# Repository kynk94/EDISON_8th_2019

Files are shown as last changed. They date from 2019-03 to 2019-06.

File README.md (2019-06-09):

# EDISON_8th_2019 - 두돈반

제 8 회 EDISON 전산설계  
  
팀명 - 두돈반  
팀장 - 강인구  
팀원 - 강인구, 기인호, 김은규, 서혁준

EDISON 8th(2019)  
Computational design Competition

## 3D 프린팅 모델


## 완성품


## 사용 부품 목록
Arduino UNO - 1 pcs  
Arduino UNO Protoshield - 1 pcs  
L298N Motor Driver - 1 pcs  
DM-CLS130TD Servo-Motor - 2 pcs  
Abrasive rod L:100mm D:5pi - 1 pcs  
과학상자 100-A Geared DC-Motor - 2 pcs  
과학상자 Gear No.106 - 2 pcs  
KOREAN : TCRT5000 IR Sensor (Mechasolution_hangul Manufatured) - 6 pcs  
TCS34725 Color Sensor - 1 pcs  
HC-SR04 Ultrasonic Sensor - 1 pcs  
1300mah LiPo Battery - 1 pcs  

## 동작 영상 (D-1) (대회 당일 영상이 없음)
<a href="http://www.youtube.com/watch?feature=player_embedded&v=sRzWvdurW9Q" target="_blank">
 IMAGE ALT TEXT HERE
</a>

## 대회 개요








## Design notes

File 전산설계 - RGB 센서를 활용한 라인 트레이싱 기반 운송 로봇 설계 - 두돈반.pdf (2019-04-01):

제8회 EDISON SW 활용 경진대회

## RGB 센서를 활용한

## 라인 트레이싱 기반 운송 로봇 설계

강인구, 기인호, 김은규, 서혁준

연세대학교 기계공학과
E-mail : kynk94@naver.com, dlghrnem@yonsei.ac.kr, dhdlrkawk1@naver.com, gurwns0904@naver.com

초록 : 본 논문은 비전 센서를 사용하지 않으면서 장애물의 색깔을 인식하여

지정된 미션을 수행하는 로봇을 제작한다. 아두이노를 활용한 차량의 라인

트레이싱을 위한 센서와 장애물을 옮기기 위한 메커니즘의 최적 설계를 수행한

모델을 제안한다.

1.서론

본 연구에서는 크게 운송을 위한 집게 형상
설계와 라인 트레이싱을 위한 센서 설계, 두
부분의 최적 설계를 제시한다. EDISON에서
제공하는 소프트웨어를 활용하여 안정적으로
운송이 가능한 운송 로봇을 설계한다. 또한
구동 시 고려해야하는 변수들을 직접 만든
프로그램을 활용하여 최적의 방식을 찾고,
이를 이용해 로봇의 설계를 진행한다.
본 논문의 구성은 다음과 같다. 2장에서
운송 로봇 설계 과정을 설명하고, 3장에서는
라인 트레이싱 제어, 색 인식과 관련된
센서들의 선정 및 설계 방법을 소개하고,
마지막으로 | 결론 | 및 | 논의사항에 | 대해서
서술한다.

2.운송 로봇 설계

### 2.1 집게 메커니즘

본 연구의 주 목표 및 설계 조건, 그리고
제작 및 분석 결과는 다음과 같다.
1) 주 목표 및 설계 조건
본 연구는 RGB센서와 아두이노를 활용한

선을 따라 자율 주행하는 라인 트레이싱
기반의 운송 로봇 설계를 주제로, EDISON이 제공하는 여러 소프트웨어들과 다른 부가적인
프로그램들을 | 활용하여 | 빠르게 | 미션을
수행하면서 | 안정적으로 | 라인 | 트레이싱을
하도록 설계하는 것을 목표로 한다.
지정된 설계 조건으로는 크게 세 가지가
있다. 첫째, 차량의 구동부는 과학상자에서
제공되는 No.100A 모터를 사용하며, 전원은 6V / 2.5A 로 공급한다. 둘째, 로봇에 사용될 기구는 과학상자 부품들, 3D프린터, 아크릴
등을 활용해 제작하며, 기구의 크기는 400mm x 400mm x 400mm 이내로 제작한다. 셋째,
제어부는 | 아두이노를 | 기반으로 | 제작하며,
센서는 총 15만원 이내에서 사용할 수 있다.
2) 모델링 결과

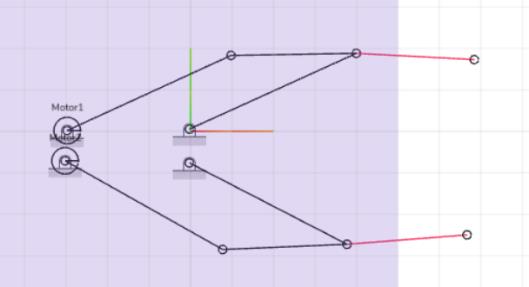
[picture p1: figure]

Figure 1. m.Sketch 링크 메커니즘

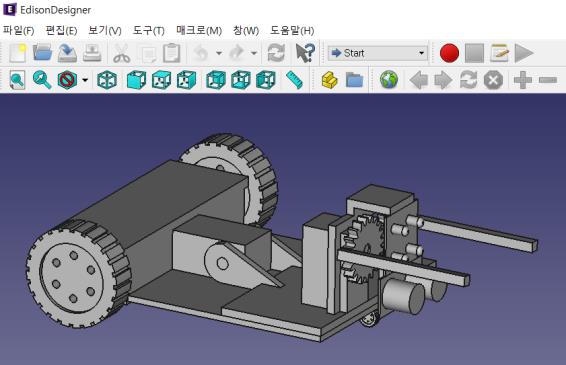
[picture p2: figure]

Figure 1. EDISON desginer 메커니즘

### 3. 로봇 센서 설계

### 3.1 라인트레이싱 메커니즘

본 메커니즘은 적외선 센서를 활용하여
라인 트레이싱을 하는 것이 목표이다.
1) 원리
라인 트레이싱에 필요한 최소 센서 개수는
2개이다. 이와 같은 기준으로 네 가지 경우의
수로 나누어진다. (1) 왼쪽 센서 인식, (2) 오른쪽 센서 인식, (3) 두 센서 모두 인식X, (4) 두 센서 모두 인식 이렇게 4가지 경우로
구분된다. 먼저 (1)의 경우는 차체의 왼쪽에서
라인을 | 인식했으므로, | 차체를 | 왼쪽으로
회전하여야 | 한다. | (2)는 | (1)과 | 반대로
오른쪽으로 회전하여야 한다. (3)은 라인이
두개의 센서 사이에 위치하므로, 직진하여야
한다. | 마지막으로 | (4)의 경우 정지하거나,
갈림길에서 원하는 특정 길을 선택할 수 있다.

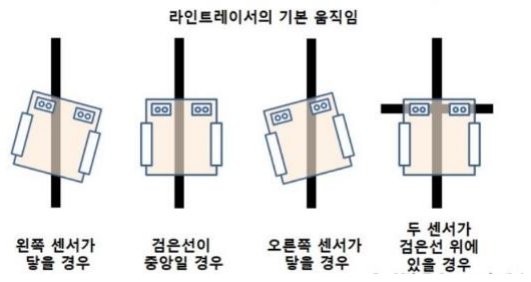
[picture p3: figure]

Figure 3. 라인 트레이싱 기본 원리

2) 알고리즘 설계
본 연구에서는 총 다섯개의 적외선 센서를
사용하여 | 아래의 | 메커니즘으로 | 라인
트레이싱을 하였다.
총 4가지 경우의 수로 나누어 설계하였다.
첫번째로, 3번 센서가 인식이 된 상태에서 2번 센서가 인식이 되면 차량이 라인의 오른쪽에
치우쳐져 있는 상태이므로 좌회전을 하였다.
4번의 센서가 인식이 되면 반대로 우회전을
하였다. 또 3번 센서만 인식되면 라인에
알맞게 있는 상태이므로 직진을 하였다. 모든
센서가 동시에 인식되는 미션 B의 끝과
라인으로 복귀할 때 만나는 교차로의 경우
서로 다른 행동을 해야하기 때문에, 모든
센서가 동시에 들어오는 첫 1회만 정지하고
그 다음은 좌회전하도록 설계하였다. 또는
모든 센서가 인식이 되지 않는 미션 C의
끝에서는 라인이 끝나는 지점이므로 정지를
하였다.

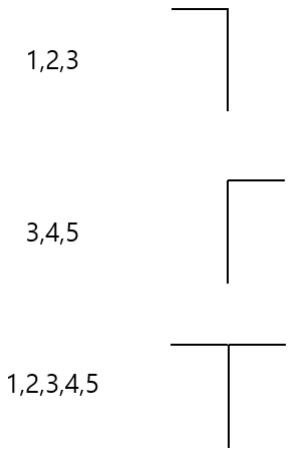
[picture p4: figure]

Figure 4. 교차로 인식 메커니즘

교차로를 인식할 때의 메커니즘은 총 3가지
경우의 수로 나누어 설계하였다. 1,2,3 센서만 인식이 되는 경우에 왼쪽 교차로로 인식을
하였다. 3,4,5 센서만 인식이 되는 경우에
오른쪽 교차로로 인식을 하였다. 마지막으로
모든 센서가 인식이 되는 경우에 T자형
교차로로 인식을 하였다.

### 3.2 RGB 센서 메커니즘

본 | 메커니즘은 | RGB | 센서를 | 이용하여
장애물의 색을 인식하고, 그에 따라 지정된
미션을 수행하는 것이 목표이다.
1) 원리
본 연구에서는 TCS230 센서를 사용하였다.
이 TCS230은 8 x 8 어레이의 포토 다이오드를 사용하여 컬러 빛을 감지한다. 그런 다음 전류
- 주파수 변환기를 사용하여 포토 다이오드의
판독 값을 광 강도에 정비례하는 주파수의
구형파로 변환한다. 마지막으로 연결되어 있는
Arduino 보드를 사용하여 구형파 출력을 읽고 색을 인지 할 수 있다.

Figure 5. TCS320 센서 작동 원리

2) 알고리즘 설계
본 | 연구에서는 | TCS230 | 센서를 | 집게
메커니즘과 가까이 배치하여 색을 앞에서 인식
할 수 있도록 설계하였다. 인식한 장애물 색의
종류에 따라 각기 다른 미션을 수행하도록
하였다.
장애물이 파란색으로 인식될 경우에 라인의
왼쪽 편으로 운송하였다. 빨간색의 경우에는
오른쪽 편으로 운송하였다.

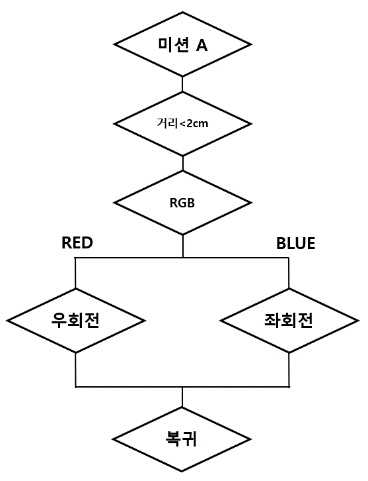
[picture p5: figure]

Figure 6. 임무 A 수행 flow chart

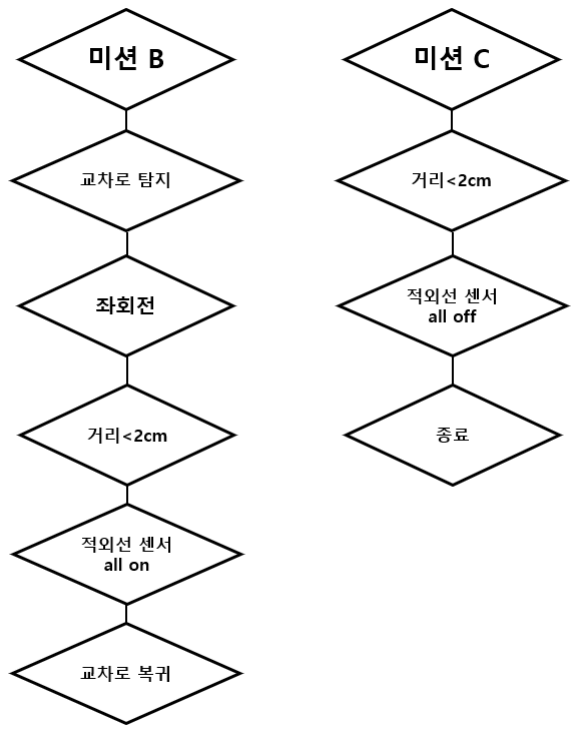
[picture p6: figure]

Figure 7. 임무 B, C 수행 flow chart

### 3.3 위치 제어 메커니즘

본 메커니즘은 엔코더를 모터에 장착하여
정확한 이동 거리를 측정하며, 초음파센서를
통해 장애물과의 거리를 감지한다. 각 모터의
성능이 다르므로 정확하게 직진을 하거나
정확하게 90도를 회전하도록 제어하는 것이
목표이다.
1) 제어 원리(PID제어)

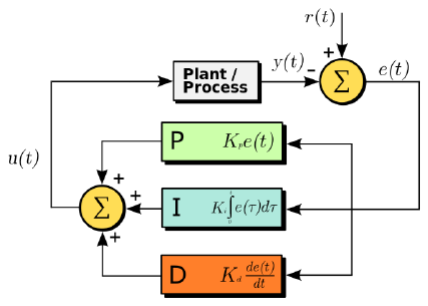
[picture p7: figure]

Figure 7. PID 제어 flowchart

PID 제어기는 제어 변수와 목표 사이의
오차에 | 근거하여 | 출력이 | 기준 | 전압을
유지하도록 하는 피드백 제어의 일종이다.

2) 모터 제어 방안
본 연구에서는 엔코더와 PID제어를 사용해
모터의 속도를 정확하게 제어하여 차체를
원하는 곳으로 위치 시킬 수 있다. 이는
정확한 직진 주행을 수행하거나 일정 거리를
이동했다가 다시 돌아올 때 용이하다.

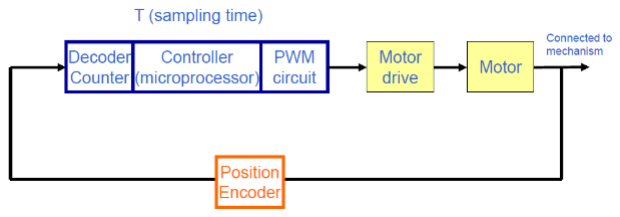
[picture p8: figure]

Figure 8. 엔코더를 적용한 모터 제어 flow chart

결과 및 논의

본 연구는 EDISON에서 제공한 다양한
프로그램들을 활용하여 RGB 센서를 이용한
라인 트레이싱 기반의 운송 로봇 설계를
하였다. 3D 형상을 설계하고, 과학상자 부품과 3D 프린터를 활용하여 제작하였다. 적외선
센서를 이용한 라인 트레이싱을 활용하여
차량이 자율 주행할 수 있도록 하였다. 이 때
적외선 | 센서의 | 개수와 | 간격을 | 조정하며
최적화를 | 하고 | 있는 | 중이다. | 또한 집게
메커니즘의 안정성을 위해서 기어 잇수나
구조를 조정하고 있다.
본 | 연구를 | 진행하며 | EDISON의 | 여러
프로그램들을 | 사용해보았다. | 프로그램의
방식이 사용자 친화적이며 직관적이어서 처음
사용해보는 사람들도 쉽게 이해하며 이용할
것으로 예상한다. 또한 많은 용량을 필요로
하는 | 프로그램들에 | 비해 | EDISON의
‘m.Sketch’의 경우 설치없이 웹을 기반으로 사용 가능하기 때문에 접근하기 쉽다는 장점이
돋보인다.

감사의 글

본 논문은 정부(과학기술정보통신부)의 재원
으로 한국연구재단 첨단 사이언스·교육 허브
개발 사업의 지원을 받아 수행된 연구임(NRF-

2011-0020576)
논문을 제작하며 고생한 네 명의 팀원에게
스스로 감사의 말을 전함.

참고문헌

[1]
https://m.blog.naver.com/PostView.nhn?blogId=smartsteam&logNo=220633642867&proxyReferer=https %3A%2F%2Fwww.google.co.kr%2F 네이버 블로그 웹사이트. (Website)
[2] 민병권, Mechatronics, (2018) April 10; Yonsei Univ.

Seoul, Korea (Conference Proceedings)

[3] | https://howtomechatronics.com. | How | to
mechatronics 웹사이트. (Website)

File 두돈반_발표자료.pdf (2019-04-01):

# 두돈 반

강인구
기인호
김은규
서혁준

Simple is the Best

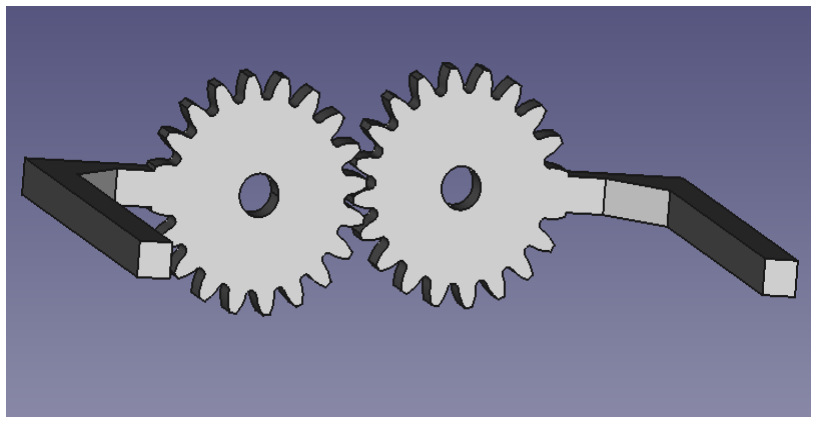
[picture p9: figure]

## Mechanism

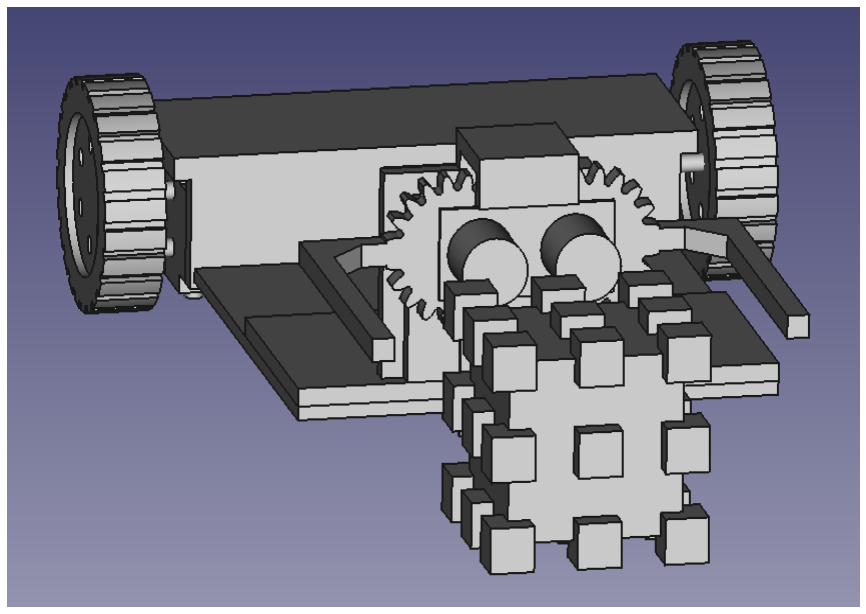
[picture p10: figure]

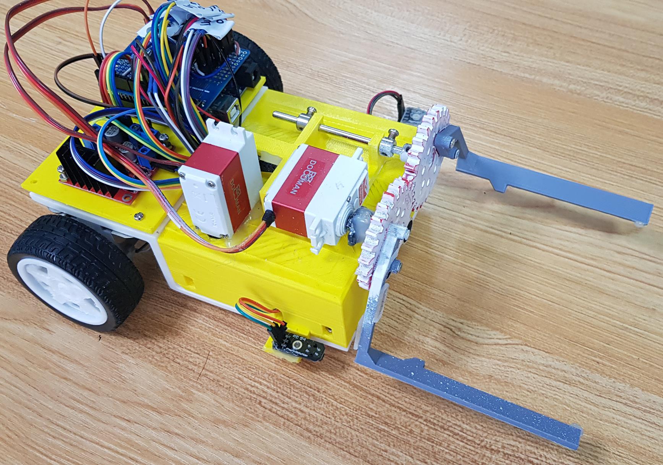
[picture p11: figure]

## Manufacture

## Sensors

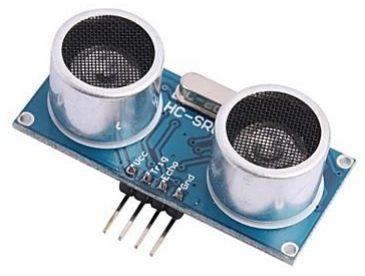
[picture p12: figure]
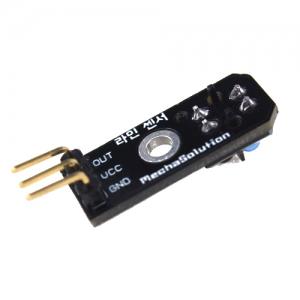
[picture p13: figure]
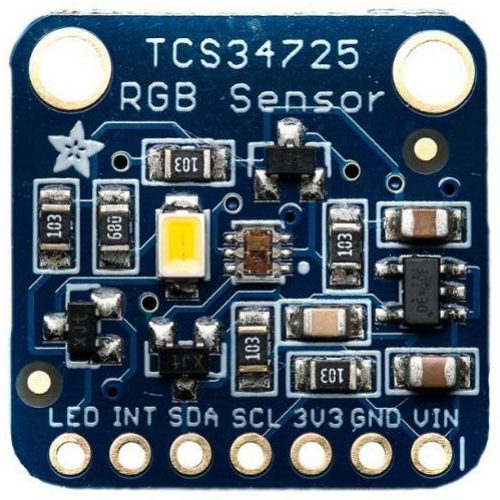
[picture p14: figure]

Problem | 라인 트레이싱, 큐브 거리 인식, 색 인식
Solution | IR 센서, RGB 센서, 초음파 센서
IR | RGB | Ultrasonic

## Motor

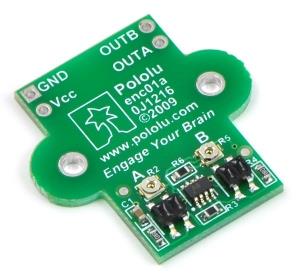
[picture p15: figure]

## Encoder

양쪽 모터의 출력 차이가 생길 경우 직진 운행이 불가능할 수도 있다.

엔코더를 사용하여 양쪽 모터의 rpm 수를 동일하게 맞추도록 한다.

Problem

Solution

## Motor Encoder

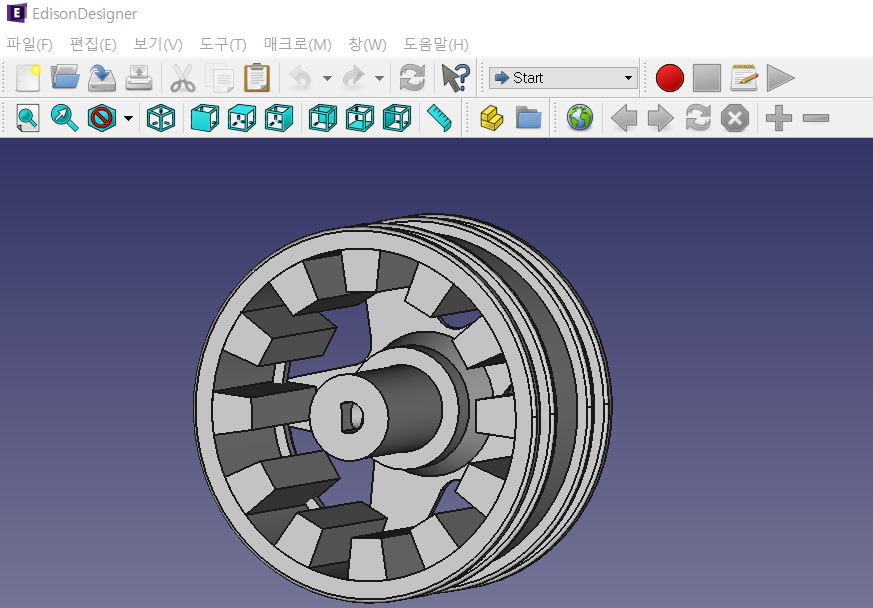
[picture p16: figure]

## 광학 엔코더를 사용하여 양쪽 바퀴 rpm 측정

## Motor

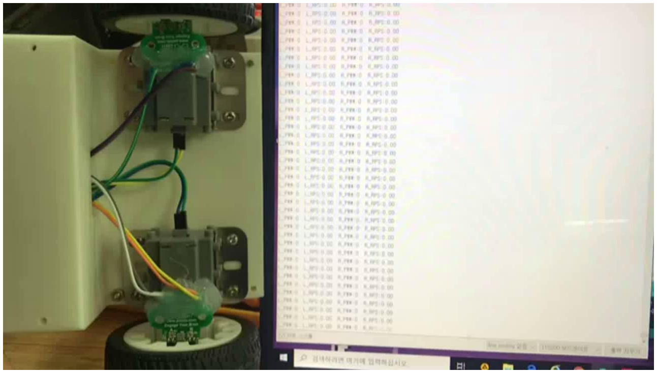
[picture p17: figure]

## Encoder

## PID Control

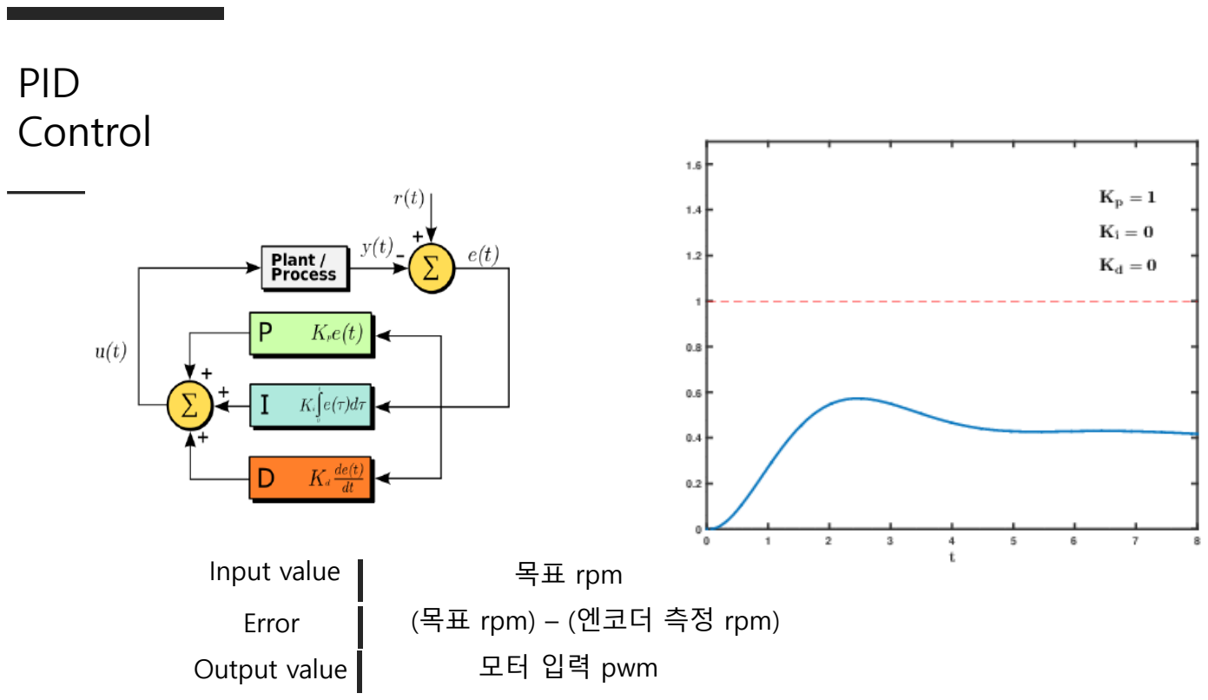
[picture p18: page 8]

Input value

Output value

목표 rpm

Error | (목표 rpm) – (엔코더 측정 rpm)
| 모터 입력 pwm

## Line tracing

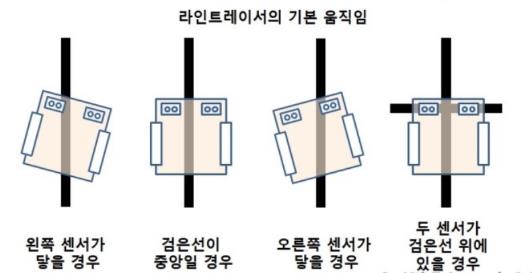
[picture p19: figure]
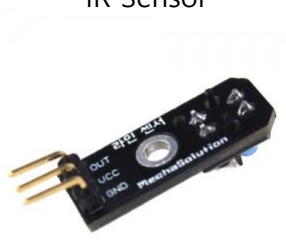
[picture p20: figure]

IR Sensor

Algorithm | 장애물

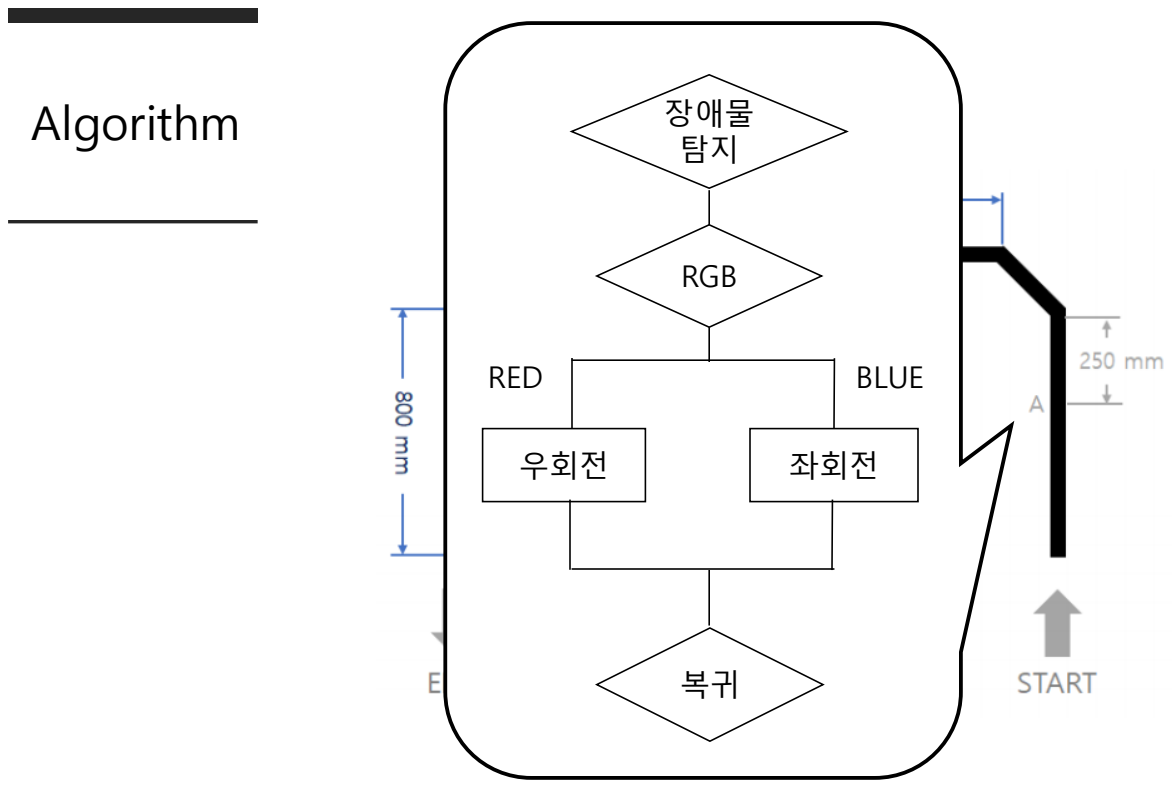
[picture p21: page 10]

탐지

RGB

우회전 | 좌회전

복귀

RED | BLUE

## Algorithm

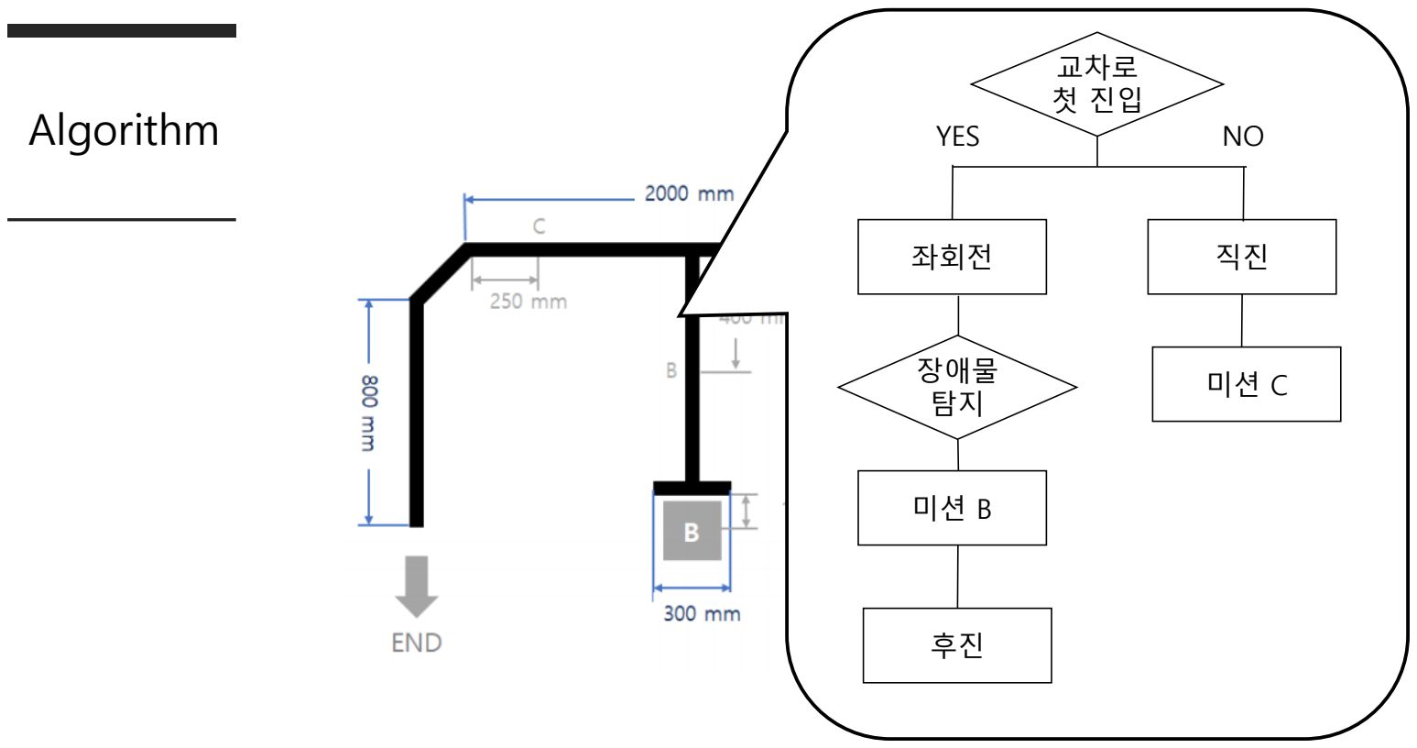
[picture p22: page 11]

교차로 첫 진입

장애물
탐지
좌회전 | 직진

미션
C

미션
B

후진

YES | NO

## Result

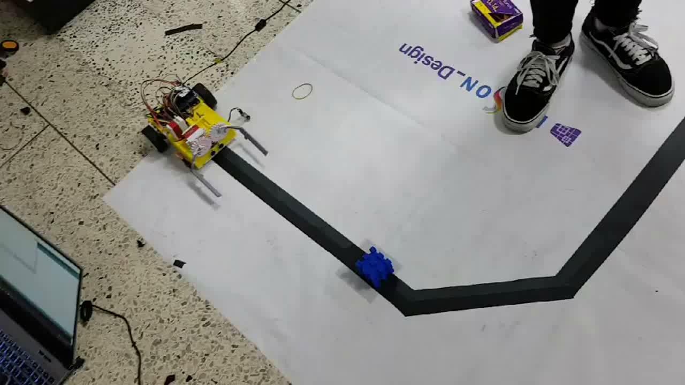
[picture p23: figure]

# The End

Thanks for watching

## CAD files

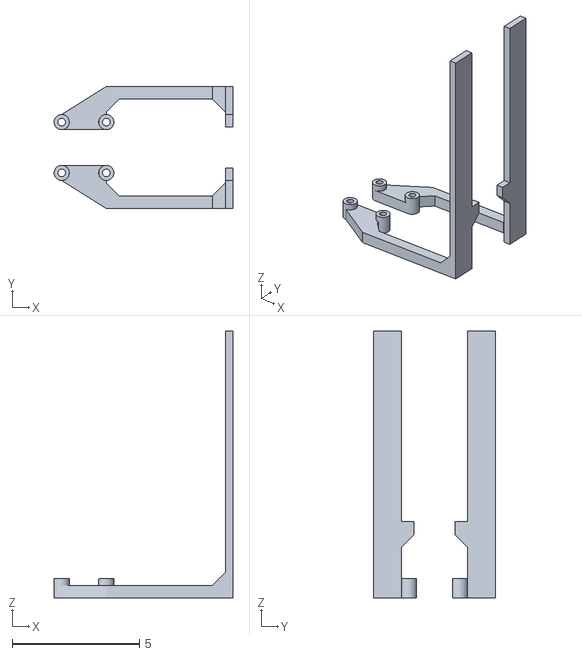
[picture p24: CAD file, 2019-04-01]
STL_files/arm.stl
7.03 x 4.80 x 10.5

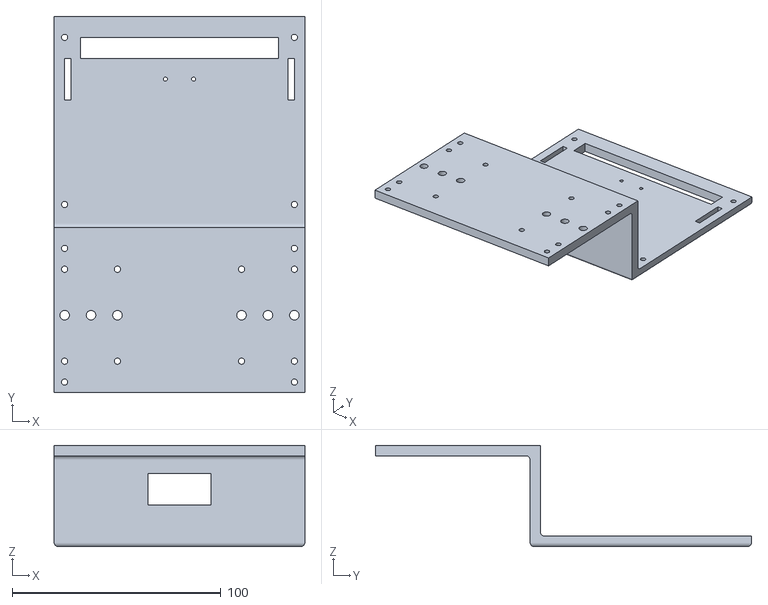
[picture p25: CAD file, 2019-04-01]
STL_files/base.stl
120.0 x 180.0 x 48.5

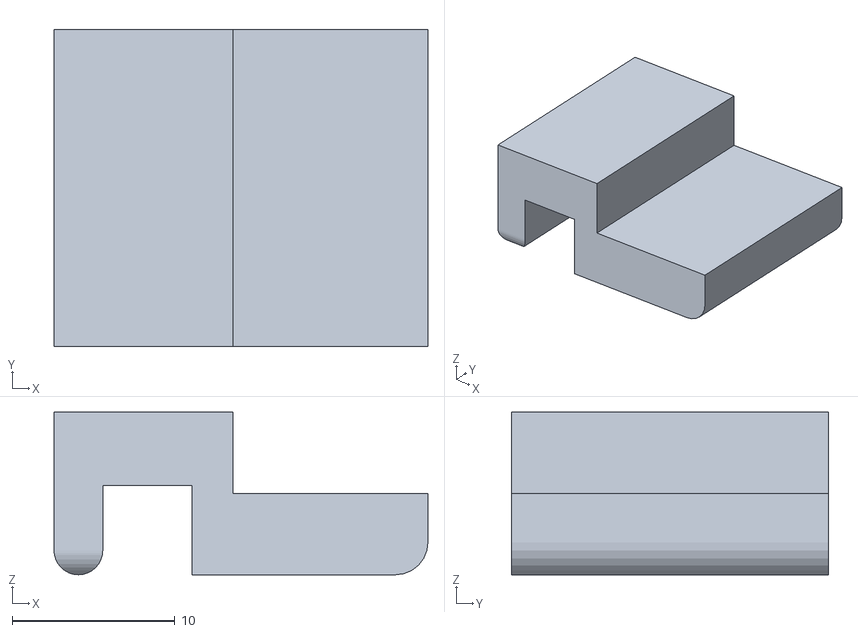
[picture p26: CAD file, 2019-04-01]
STL_files/wing.stl
23.0 x 19.5 x 10.00

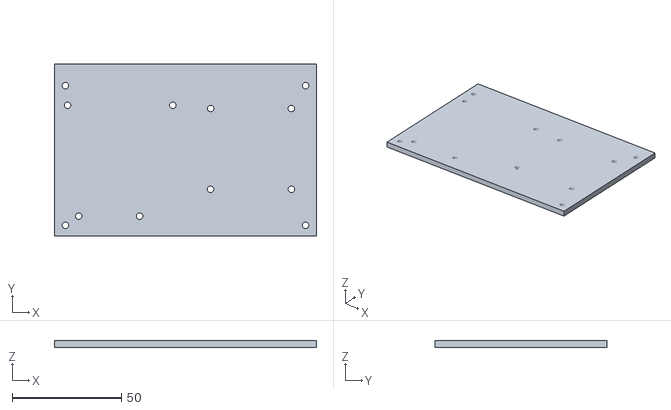
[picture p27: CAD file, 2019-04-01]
STL_files/up_cover.stl
120.0 x 79.0 x 3.00

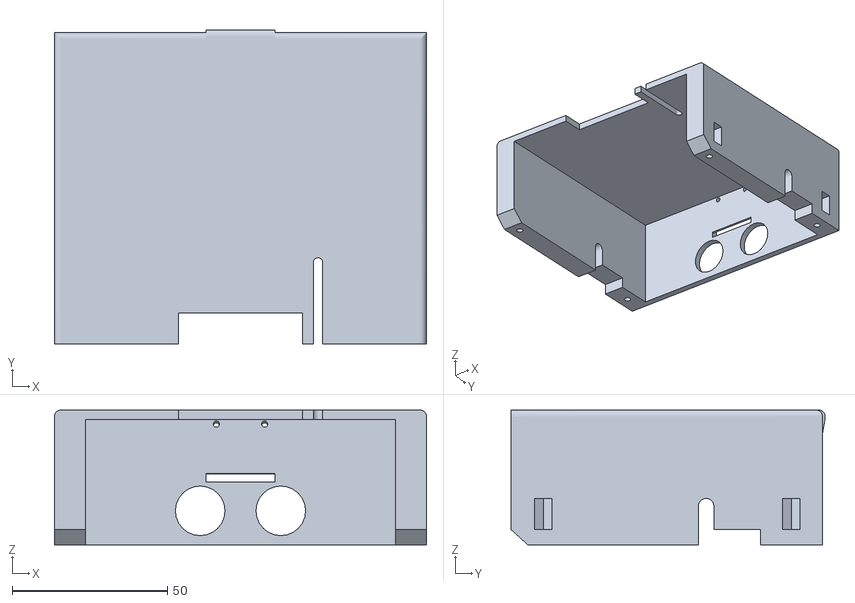
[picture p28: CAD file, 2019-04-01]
STL_files/cover.stl
120.0 x 101.4 x 43.5

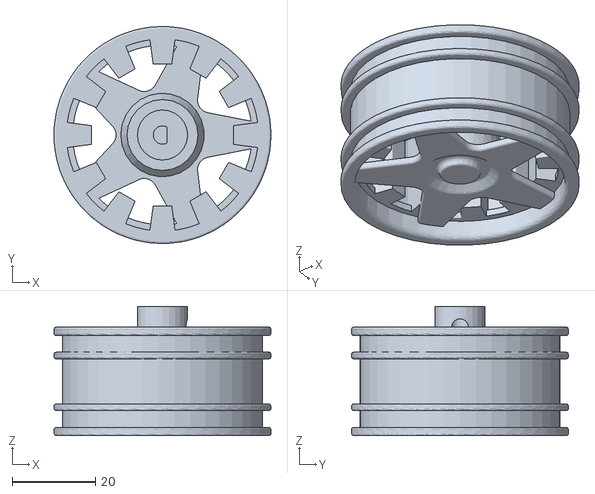
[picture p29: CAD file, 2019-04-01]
STL_files/wheel.stl
52.0 x 52.0 x 31.0

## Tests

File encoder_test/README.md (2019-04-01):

# Encoder  
  
## 사용한 인코더 - Encoder for Pololu Wheel 42x19mm  
https://www.pololu.com/product/1217

<a href="http://www.robotoid.com/appnotes/circuits-quad-encoding.html">
 
</a>

양쪽 바퀴의 RPM을 측정하여 PID 제어를 하기 위해 광학 인코더를 사용한다.  
각 인코더에 있는 2개의 센서에서 Wheel에 있는 12개의 톱니 요철 변화에 따라서 Pulse가 발생하며,  
이 Pulse가 단위시간에 몇회 발생하는지 감지하여 속도를 측정하였다.  
## Wheel  
#### 3D model  
  
#### Printed Wheel


판매처에서 Wheel은 제공하지 않고 Encoder만 제공하였으며, 또한 우리 팀 작품의 조건에 부합하지 않았다.  
때문에 Wheel의 경우 직접 모델링하여 3D 프린팅하였다.  

## 동작 영상
<a href="http://www.youtube.com/watch?feature=player_embedded&v=ZOc87ReWXjc" target="_blank">
 IMAGE ALT TEXT HERE
</a>

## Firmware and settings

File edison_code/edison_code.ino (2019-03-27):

#include "Adafruit_TCS34725.h"
/*tcs에 센서를 선언*/
Adafruit_TCS34725 tcs = Adafruit_TCS34725(TCS34725_INTEGRATIONTIME_24MS, TCS34725_GAIN_4X);
#include <Servo.h>
//pwm pin = 3,5,6,9,10,11
#define servo_gear_pin 3
#define servo_up_pin 5

#define motorL 6
#define motorL_F 8
#define motorL_B 7
#define motorR_F 9
#define motorR_B 10
#define motorR 11

#define TRIG 12
#define ECHO 13

#define ir1 2
#define ir2 A0
#define ir3 A1
#define ir4 A2
#define ir5 A3
#define ir6 4

Servo servo_gear;
Servo servo_up;

/*******************서보모터**************************/
float gear_first = 120;
float gear_limit = 23;
float up_first = 36;
float up_limit = 57;
/*******************인풋**************************/
int up_sign=0, gear_sign=0;
float input_gear=gear_first, input_up=up_first, b_input_gear=gear_first, b_input_up=up_first;
float L_output=0, R_output=0;
float L_PWM=0, R_PWM=0;
float error=0;
float start_time=0,loop_time=0;
int ir1_a,ir2_a,ir3_a,ir4_a,ir5_a,ir6_a;
int ir1_s,ir2_s,ir3_s,ir4_s,ir5_s,ir6_s;
float r=0,g=0,b=0;
float rps4_Lm = -63, rps4_Rm = -48;
float rps3_Lm = -52, rps3_Rm = -39;
float rps2_Lm = -42, rps2_Rm = -32;
float rps1_Lm = -32, rps1_Rm = -26;
float rps1_L = 30, rps1_R = 25;
float rps2_L = 39, rps2_R = 32;
float rps3_L = 47, rps3_R = 37;
float rps4_L = 60, rps4_R = 48;
float rps5_L = 79, rps5_R = 58;
float rps6_L = 107, rps6_R = 75;
String total_state, drive_state;
/**********************************/
float Kp=7;
float Ki=0.5;
float Kd=1;
float L_I_val=0,L_D_val=0,R_I_val=0,R_D_val=0;
float distance = 10;
int T_count=0,Acount=0,Bcount=0,first_drive_count=0,linecase=0;
int check_start=0;
int grabMode=0;
float case_d=6.5;

void setup() {
  Serial.begin(115200);
  while(!Serial);
  Serial.println("Ready");
  /*라인센서*/
  pinMode(ir1, INPUT);
  pinMode(ir2, INPUT);
  pinMode(ir3, INPUT);
  pinMode(ir4, INPUT);
  pinMode(ir5, INPUT);
  pinMode(ir6, INPUT);
  /*초음파센서*/
  pinMode(TRIG, OUTPUT);
  pinMode(ECHO, INPUT);
  /*모터*/
  pinMode(motorL, OUTPUT);
  pinMode(motorR, OUTPUT);
  pinMode(motorL_F, OUTPUT);
  pinMode(motorL_B, OUTPUT);
  pinMode(motorR_F, OUTPUT);
  pinMode(motorR_B, OUTPUT);
  digitalWrite(TRIG,LOW);
  digitalWrite(ECHO,LOW);
  servo_gear.attach(servo_gear_pin);
  servo_up.attach(servo_up_pin);
  servo_gear.write(gear_first);
  servo_up.write(up_first);
  digitalWrite(motorR_F,LOW);
  digitalWrite(motorR_B,LOW);
  analogWrite(motorR,0);
  digitalWrite(motorL_F,LOW);
  digitalWrite(motorL_B,LOW);
  analogWrite(motorL,0);
  tcs.begin();
  tcs.setInterrupt(true);
  delay(15);
  Serial.println("start");
}

void loop() {
  while(check_start==0){
    sensor_state();
    L_PWM=rps4_L;
    R_PWM=rps4_R;
    motor_control();
    if(drive_state=="0100"||drive_state=="0110"||drive_state=="0010")check_start=1;
  }
  start_time = micros();
  sensor_state();
  drive();
  
  distance = ultra_sonic();
  if(Acount==0)case_d=9.5;
  else if(Acount==1 && Bcount==0)case_d=6.5;
  else if(Acount==1 && Bcount==1)case_d=9.5;
  if(distance<case_d && grabMode==0){
    stop_bot();
    ultra_sonic();
    delay(30);
    if(Acount==0){
      grab();
      RGB_sense();
      if(r>83 && b <85){        
        missionA_red();
      }
      else if(r<=83 && b>=85-distance){
        missionA_blue();
      }
      Acount=1;
    }
    else grab();
  }
  T_check();
  /*
  Serial.print("IR1:"+String(ir1_a));
  Serial.print(" IR2:"+String(ir2_a));
  Serial.print(" IR3:"+String(ir3_a));
  Serial.print(" IR4:"+String(ir4_a));
  Serial.print(" IR5:"+String(ir5_a));
  Serial.println(" IR6:"+String(ir6_a));
  Serial.println(" Distance:"+String(distance));
  */
  loop_time = micros() - start_time;
}

void T_check(){
    if(String(ir1_s)+String(ir2_s)+String(ir3_s)+String(ir6_s)=="1110"){
    delay(150);left_turn();
    if(T_count==0){
      L_PWM=rps3_Lm-20;
      R_PWM=rps3_Rm-16;
      motor_control();
      delay(150);
      distance=15;
      L_PWM=rps4_L-5;
      R_PWM=rps4_R;
      motor_control();
      delay(50);
      sensor_state();
    }
  }
  if((String(ir1_s)+String(ir6_s)=="11")||(String(ir1_s)+String(ir5_s)=="11")||(String(ir2_s)+String(ir6_s)=="11")){
    if(T_count==0){
      if(Bcount==0){
        //Serial.println("BBB");
        L_PWM=rps4_L;
        R_PWM=rps4_R;
        motor_control();
        delay(50);
        stop_bot();
        ungrab();
        Bcount=1;
      }
      T_count+=1;
      L_PWM=rps3_Lm-23;
      R_PWM=rps3_Rm-18;
      motor_control();
      delay(600);
      if(Bcount==0)redLeftTurn();
      else if(Bcount==1)left_turn();
    }
    else if(T_count==1){
      delay(150);left_turn();
      distance=15;
      L_PWM=rps4_L;
      R_PWM=rps4_R;
      motor_control();
      delay(10);
    }
  }
}

void drive(){
  /*왼쪽이 더 약함*/
  float want_rps_L,want_rps_R;
  /*
  if(drive_state="0000"&&first_drive_count==0){
    while(1){
      first_drive_count=1;
      L_PWM=rps4_L;
      R_PWM=rps4_R;
      motor_control();
      sensor_state();
      if(drive_state!="0000")break;
    }
  }*/
  if(drive_state=="1000"){
    error=-3; want_rps_L=rps4_L; want_rps_R=rps4_R; Kp=9;
    if(Bcount>=1&&grabMode==1){
      want_rps_L=rps4_L+20;
      want_rps_R=rps5_R+25;
      up_limit=55;
    }
  }
  else if(drive_state=="1100"){
    error=-2; want_rps_L=rps4_L; want_rps_R=rps4_R; Kp=9;
    if(Bcount>=1&&grabMode==1){
      want_rps_L=rps4_L+20;
      want_rps_R=rps5_R+25;
      up_limit=55;
    }
  }
  else if(drive_state=="0100"){
    error=-1; want_rps_L=rps5_L; want_rps_R=rps5_R; Kp=9;
  }
  else if(drive_state=="0110"){
    error=0; want_rps_L=rps5_L; want_rps_R=rps5_R; Kp=10;
  }
  else if(drive_state=="0010"){
    error=1; want_rps_L=rps5_L; want_rps_R=rps5_R; Kp=9;
  }
  else if(drive_state=="0011"){
    error=2; want_rps_L=rps4_L; want_rps_R=rps4_R; Kp=9;
  }
  else if(drive_state=="0001"){
    error=3; want_rps_L=rps4_L; want_rps_R=rps4_R; Kp=9;
  }
  L_PWM = calculate_pid(error,L_I_val,L_D_val,L_output)*1.3 + want_rps_L;
  R_PWM = calculate_pid(-error,R_I_val,R_D_val,R_output) + want_rps_R;
  motor_control();                                                                                  
}

void left_turn(){
  L_PWM = rps3_Lm-25;
  R_PWM = rps5_R;
  motor_control();
  delay(600);
  while(1){
    sensor_state();
    if(total_state=="000110"||total_state=="000100")break;
  }
}

void right_turn(){
  L_PWM = rps3_L+13;
  R_PWM = rps3_Rm-10;
  motor_control();
  delay(1000);
}

float calculate_pid(float error,float &I_val,float &D_val, float output){
  float P_val = error*Kp;
  float previous_error;
  float I_const=20;
  I_val += Ki*error*loop_time/1000000;
  if(I_val>I_const)I_val=I_const;
  else if(I_val<-I_const)I_val=-I_const;
  D_val = (error-previous_error)*Kd*loop_time/1000000;
  output = P_val;
  output += I_val+D_val;
  previous_error=error;
  return output;
}

void motor_control(){
  if(L_PWM>255)L_PWM=255;
  else if(L_PWM<-255)L_PWM=-255;
  if(R_PWM>255)R_PWM=255;
  else if(R_PWM<-255)R_PWM=-255;
  if(L_PWM>=0){
    digitalWrite(motorL_F, HIGH);
    digitalWrite(motorL_B, LOW);
    analogWrite(motorL, abs(L_PWM));
  }
  else if(L_PWM<0){
    digitalWrite(motorL_F, LOW);
    digitalWrite(motorL_B, HIGH);
    analogWrite(motorL, abs(L_PWM));
  }
  if(R_PWM>=0){
    digitalWrite(motorR_F, HIGH);
    digitalWrite(motorR_B, LOW);
    analogWrite(motorR, abs(R_PWM));
  }
  else if(R_PWM<0){
    digitalWrite(motorR_F, LOW);
    digitalWrite(motorR_B, HIGH);
    analogWrite(motorR, abs(R_PWM));
  }
}

void RGB_sense(){
  uint16_t clear,red, green, blue;
  tcs.setInterrupt(false);
  delay(30);
  tcs.getRawData(&red,&green,&blue,&clear);
  tcs.setInterrupt(true);
  uint32_t sum = clear;
  r=red;r/=sum;
  g=green;g/=sum;
  b=blue;b/=sum;
  r*=256;g*=256;b*=256;
}

void ir_read(){
  ir1_a=digitalRead(ir1);
  ir2_a=analogRead(ir2);
  ir3_a=analogRead(ir3);
  ir4_a=analogRead(ir4);
  ir5_a=analogRead(ir5);
  ir6_a=digitalRead(ir6);
  if(ir1_a>=1)ir1_s=1;
  else ir1_s=0;
  if(ir2_a>=100)ir2_s=1;
  else ir2_s=0;
  if(ir3_a>=100)ir3_s=1;
  else ir3_s=0;
  if(ir4_a>=100)ir4_s=1;
  else ir4_s=0;
  if(ir5_a>=100)ir5_s=1;
  else ir5_s=0;
  if(ir6_a>=1)ir6_s=1;
  else ir6_s=0;
}

void sensor_state(){
  ir_read();
  total_state = String(ir1_s)+String(ir2_s)+String(ir3_s)+String(ir4_s)+String(ir5_s)+String(ir6_s);
  drive_state = String(ir2_s)+String(ir3_s)+String(ir4_s)+String(ir5_s);
  Serial.print(total_state);Serial.print("  ");
}

float ultra_sonic(){
  digitalWrite(ECHO,LOW);
  digitalWrite(TRIG,HIGH);
  delay(2);
  digitalWrite(TRIG,LOW);
  return (pulseIn(ECHO,HIGH)*0.034/2);
}

/***************************************************/
void missionA_red(){
  sharpRightTurn();
  stop_bot();
  delay(50);
  ungrab();
  delay(50);
  redLeftTurn();
  delay(50);
  Acount=1;
}

void missionA_blue(){
  sharpLeftTurn();
  stop_bot();
  delay(50);
  ungrab();
  delay(50);
  blueRightTurn();
  delay(50);
  Acount=1;
}

void grab(){
  /*집게 오므리기*/
  for(int i=gear_first; i>gear_limit; i--){
    servo_gear.write(i);
    delay(8);
  }
  /*들어 올리기*/
  for(int i=up_first; i<up_limit; i++){
    servo_up.write(i);
    delay(5);
  }
  grabMode=1;
}

void ungrab(){
  /*내리기*/
  for(int i=up_limit; i>up_first; i--){
    servo_up.write(i);
    delay(5);
  }
  delay(10);
  /*집게 풀기*/
  for(int i=gear_limit; i<gear_first; i++){
    servo_gear.write(i);
    delay(5);
  }
  grabMode=0;
}

void stop_bot(){
  digitalWrite(motorL_F, LOW);
  digitalWrite(motorL_B, LOW);
  digitalWrite(motorR_F, LOW);
  digitalWrite(motorR_B, LOW);
  L_I_val=0;
  L_D_val=0;
  R_I_val=0;
  R_D_val=0;
}

void sharpLeftTurn(){
  L_PWM=rps3_Lm-30;
  R_PWM=rps5_R;
  motor_control();
  delay(1100);
}

void sharpRightTurn(){
  L_PWM=rps5_L;
  R_PWM=rps3_Rm-30;
  motor_control();
  delay(1000);
}
void redLeftTurn(){
  L_PWM=rps3_Lm-30;
  R_PWM=rps5_R;
  motor_control();
  delay(700);
  while(1){
    sensor_state();
    if(drive_state=="0100"||drive_state=="0010"||drive_state=="0011"){
      stop_bot()
      ;
      delay(10);
      break;
    }
  }
}

void blueRightTurn(){
  L_PWM=rps5_L;
  R_PWM=rps3_Rm-23;
  motor_control();
  while(1){
    sensor_state();
    if(drive_state=="0011"||drive_state=="0001"){
      stop_bot();
      delay(10);
      break;
    }
  }
}

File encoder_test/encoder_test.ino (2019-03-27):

#include <PololuWheelEncoders.h>
// 1rev = 48 pulse
#define encoderL_A 4
#define encoderL_B 2
#define encoderR_A 12
#define encoderR_B 13

#define motorL 6
#define motorL_F 8
#define motorL_B 7
#define motorR_F 9
#define motorR_B 10
#define motorR 11

PololuWheelEncoders enc;

float inputL=0, inputR=0;
int enc_i = 1;
float L_C = 0, R_C = 0;
float L_speed = 0, R_speed = 0;
float L_output=0, R_output=0;
int L_PWM=0, R_PWM=0;
float enc_loopL = 0, enc_loopR = 0, b_enc_loopL = 0, b_enc_loopR = 0;
/******************************왼쪽이 더 약함***************************/
float Kp_L = 0.04;
float Ki_L = 0.5;
float Kd_L = 1.2;
float Kp_R = 0.03;
float Ki_R = 0;
float Kd_R = 1;
/*********************************************************************/
float L_I_val = 0, L_D_val = 0;
float R_I_val = 0, R_D_val = 0;

float enc_time = 0,start_time=0, loop_time=0, b_loop_time=0;

void setup(){
  Serial.begin(115200);
  while(!Serial);
  enc.init(encoderR_A,encoderR_B, encoderL_A, encoderL_B);
  pinMode(motorL, OUTPUT);
  pinMode(motorR, OUTPUT);
  pinMode(motorL_F, OUTPUT);
  pinMode(motorL_B, OUTPUT);
  pinMode(motorR_F, OUTPUT);
  pinMode(motorR_B, OUTPUT);
  Serial.println("start");
  digitalWrite(motorR_F,HIGH);
  digitalWrite(motorR_B,LOW);
  analogWrite(motorR,0);
  digitalWrite(motorL_F,HIGH);
  digitalWrite(motorL_B,LOW);
  analogWrite(motorL,0);
  Serial.write(0);
  delay(15);
}

void loop(){
  start_time = micros();
  
  while(Serial.available()){
    inputL = Serial.parseFloat();
    inputR = Serial.parseFloat();
    Serial.setTimeout(10);
    enc_i = 1;
  }
  
  enc_read_by_pulse();
  loop_time = micros() - start_time;
  L_speed = L_C*100000 / loop_time;
  R_speed = R_C*100000 / loop_time;
  
  delay(100);
  
  enc_read_by_time();
  L_PWM = pid_cal(inputL, L_speed, Kp_L, Ki_L, Kd_L, L_I_val, L_D_val, L_output);
  R_PWM = pid_cal(inputR, R_speed, Kp_R, Ki_R, Kd_R, R_I_val, R_D_val, R_output);
  Serial.print("L_PWM:");Serial.print(L_PWM);Serial.print("  ");
  Serial.print("L_RPS:");Serial.print(L_speed);Serial.print("  ");
  Serial.print("R_PWM:");Serial.print(R_PWM);Serial.print("  ");
  Serial.print("R_RPS:");Serial.println(R_speed);
  motor_control();
}

void motor_control(){
  if(L_PWM>=0 && inputL!=0){
    digitalWrite(motorL_F, HIGH);
    digitalWrite(motorL_B, LOW);
    analogWrite(motorL, abs(L_PWM));
  }
  else if(L_PWM<0 && inputL!=0){
    digitalWrite(motorL_F, LOW);
    digitalWrite(motorL_B, HIGH);
    analogWrite(motorL, abs(L_PWM));
  }
  else if(inputL==0){
    analogWrite(motorL, 0);
    L_I_val = 0;
    L_D_val = 0;
    L_output = 0;
  }
  if(R_PWM>=0 && inputR!=0){
    digitalWrite(motorR_F, HIGH);
    digitalWrite(motorR_B, LOW);
    analogWrite(motorR, abs(R_PWM));
  }
  else if(R_PWM<0 && inputR!=0){
    digitalWrite(motorR_F, LOW);
    digitalWrite(motorR_B, HIGH);
    analogWrite(motorR, abs(R_PWM));
  }
  else if(inputR==0){
    analogWrite(motorR, 0);
    R_I_val = 0;
    R_D_val = 0;
    R_output = 0;
  }
}

int pid_cal(float val,float enc_speed,
            float Kp,float Ki,float Kd, float & I_val, float & D_val, float & output){
  float error = val - enc_speed;
  float previous_error;
  float P_val = Kp * error;
  
  I_val += Ki * error * loop_time/1000000;
  D_val = (error - previous_error) * Kd * loop_time/1000000;
  previous_error = error;
  output += P_val + I_val + D_val;
  if(output>255){
    output=255;
  }
  else if(output<-255){
    output=-255;
  }
  return output;
}

void enc_read_by_pulse(){
  b_enc_loopL = enc_loopL;
  b_enc_loopR = enc_loopR;
  enc_loopL = enc.getCountsAndResetM1();
  enc_loopR = enc.getCountsAndResetM2();
  L_C = (enc_loopL+b_enc_loopL);
  R_C = (enc_loopR+b_enc_loopR);
}

void enc_read_by_time(){
  if(enc_i==1){
    enc_time = start_time;
    b_enc_loopL = enc_loopL;
    b_enc_loopR = enc_loopR;
    enc_i=0;
  }
  /********enc_read**********/
  enc_loopL = enc.getCountsM1();
  if(abs(enc_loopL)>10000000){
    enc_loopL = enc.getCountsAndResetM1();
  }
  enc_loopR = enc.getCountsM2();
  if(abs(enc_loopR)>10000000){
    enc_loopR = enc.getCountsAndResetM2();
  }
  /**************************/
  float limit_time = micros()-enc_time;
  if(limit_time/1000000>0.1){
    //Serial.print(micros());
    L_C = (enc_loopL - b_enc_loopL)/48;
    R_C = (enc_loopR - b_enc_loopR)/48;
    //Serial.print(L_C);Serial.print("  ");Serial.println(R_C);
    L_speed = L_C / (limit_time/1000000); //RPS
    R_speed = R_C / (limit_time/1000000); //RPS
    enc_i=1;
  }
}

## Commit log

2019-03-27 encoder test
2019-03-27 RGB sensor test code
2019-03-27 Servo motor test
2019-04-01 Encoder Updater
    [wheel.stl]
2019-04-01 STL Files
    [arm.stl, base.stl, cover.stl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]
2019-04-01 발표자료
